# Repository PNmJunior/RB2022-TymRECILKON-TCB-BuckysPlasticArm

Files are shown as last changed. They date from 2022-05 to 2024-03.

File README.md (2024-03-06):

# Článek o vývoji robota BuckysPlasticArm

Robot BuckysPlasticArm je pojízdný robot s manipulačním ramenem. Sestavil jsem si ho, abych si vyzkoušel práci s webovým  serverem umístěným v ESP32 (ESP32DevKitV1 [^11]), který přes webserver  umožňuje řídit pohyb robota s osmi DC motory. Webserver poskytuje v lokální sítí webovou službu, přes  kterou jde z více webových prohlížečů najednou ovládat robota. 

Prakticky jsem si funkčnost robota ověřoval na soutěži Robotický den 2022 a 2023. [^2][^3]

## Historie projektu

### 1.Etapa 
S projektem jsem začal v březnu 2022 a mým cílem byl Robotický den 2022 konající se 5. a 6. června. [^1] Jako základ jsem vybral projekt s nazývem „ESP32 Web Server (WebSocket) with Multiple Sliders: Control LEDs Brightness (PWM).“ od „Random Nerd Tutorials“, který jsem našel na internetu, a který jsem upravil pro své potřeby.[^3] Šlo o ovládání tří parametrů LEDek. Zvětšil jsem množství ovládaných parametrů na osm. Každý ovládací parametr řídil jeden motor. Do původní webové stránky [^3] jsem přidal jak nové horizontální, tak i vertikální slidery (ovládací posuvný prvek v HTML(```<imput type="range">```)).[^10] Zjistil jsem, že z Androidů lze ovládat dva slidery najednou, zatím  co na počítači limitovaného  myší, šlo ovládat jen jeden slider. Můj plán byl umožnit řídit robota ze čtyř mobilních zařízení najednou v reálném čase pomoci týmů lidí. Kvůli řízení v reálném čase, jsem musel minimalizovat množství posílaných dat. Díky tomu jsem se dostal na odezvu robota v řádech desítek milisekund. Změnil jsem typ http serveru ze synchronního na asynchronní.

Na soutěži jsem si ověřil, že řízení pomocí více lidí je špatný nápad, kvůli jejích nutné vzájemné souhře.

### 2.Etapa
Technologie webserveru v ESP32 mě zaujala, a tak jsem se rozhodl pokračovat ve vývoji. Pustil jsem se do velké přestavby konstrukce robota, hardwaru a softwaru. Vytvořil jsem si jednoduchý ovládací panel, který mi umožňoval výběr WiFi a  zadání hesla pomoci enkodéru pro připojení k lokální síti. Pomoci segmentového LED displeje robot informoval o vlastní aktuální IP adrese v lokální síti. Vytvořil jsem si vlastní komunikační protokol mezi serverem a klienty. Přidal jsem do zobrazení webu čtyři joysticky se synchronizací (každý vidí, co dělají ostatní).[^7] Synchronizace sliderů byla už z původního projektů.[^3] Kód pro joystick, který byl napsaný v JavaScriptu, hýbal s obrázkem páčky. ESP32 převádělo pohyby joysticků na pohyb sliderů. Díky tomu šlo jedním kliknutím ovládat až dva motory najednou. Tím se mi snížil počet lidí s telefonem k ovládaní robota na dva. 

### 3.Etapa - Fyzické joysticky
Rozhodl jsem se, že umožním řízení zmíněných osmi motorů pomoci jednoho člověka. Pro tento účel jsem vyrobil dvojici fyzických joysticků (pro každou ruku), kde se zápěstím ovládá dolní joystick a druhý/horní joystick se ovládá pomoci palce. 

Po té jsem začal řešit spojení s robotem. Ano, šlo to jednoduše vyřešit dalším ESP32, ale to bych si nevyzkoušel nové technologie, a proto jsem se rozhodl, že použiju WebUSB.[^4] Pomoci desky Bluepill(deska s čipem ARM STM32 STM32F103C8 [^12]) jsem chtěl komunikovat s webovým klientem v prohlížeči právě přes USB. Zde jsem narazil na překážku v podobě bezpečnosti, kde bylo podmínkou použití protokolu https. Celý projekt do této doby fungoval přes http. Po nastudování dokumentace a různých diskusí jsem došel k názoru, že přeprogramovat ESP32 na https server by bylo možné. Ale mnohonásobně by se tím zvýšila doba odezvy až na sekundy. Zároveň by se snížil počet možných webových klientů z osmi na maximálně čtyři, co je na hranici plánovaného používaní.[^8] [^9] K řešení problému s bezpečností nepřispělo ani nahrávaní stránek z disku. Nakonec jsem musel použit aplikaci, která umožňovala převádět komunikaci z USB na Telnet napsané v Javě.[^5] Tento koncept jsem použil a zprovoznil, ale doba odezvy byla vysoká a tak jsem přeprogramoval aplikaci pro simulaci klienta.[^6] Tím jsem maximálně snížil dobu odezvy na pohyb joysticků. Můj protokol nebyl navržen pro stream, ale pouze pro paketovou přepravu. To mělo za následek, že jsem musel vyřešit na straně aplikace rozpoznávání zamýšlených paketů.

### Testování webu na konci 2.etapy a v průběhu celé 3.etapy 
Projekt jsem ladil pouze na prohlížeči Google Chrome pro platformy Windows a Android. K tomu se mi občas objevila možnost si kód otestovat na jiných zařízeních, platformách a prohlížečích. Díky tomu jsem zjistil několik zajímavých informací z pohledu kompatibility kódu. Při testovaní jsem se zaměřoval na funkce  sliderů a  softwarových joysticků. Testy s Mac a IOS byly prováděny pouze na prohlížeči Safari. U Androidu jsem provedl testovaní na Webview, Google Chrome a Firefox. Na Windows jsem to otestoval na  Webview, Google Chrome, Firefox a Edge. Na Linuxech jsem testoval Google Chrome a Firefox. Podle očekávaní se slider zobrazoval na různých prohlížečích trochu jinak(různá implementace HTML prvku).[^11] Překvapil mě rozdíl podpory zobrazení horizontálních a vertikálních sliderů v rámci stejného prohlížeče. Dokonce na Firefoxu mi vertikální slidery vůbec nefungovaly. Je ale důležité upozornit, že joysticky (manipulovaní s obrázkem) vždy fungovaly na všech prohlížečích správně a měly ten samý vzhled a chování.[^7]

Nalezl jsem článek, který popisuje tuhle problematiku. [^13] 

### 4.etapa
Znova jsem celého robota přestavěl konstrukčně a ještě před soutěží Robotický den 2023 [^2] jsem implementoval funkce pro kontrolu spojení. Na soutěži mi robot kvůli neustálé detekci rušení spojení přerušoval pohyb. Bohužel neměl jsem čas dostatečně vyladit tuhle kontrolu.

### Finální zakončení projektu
Po soutěži jsem vytvořil github větev def2024, kde je program bez funkcí kontroly spojení.

Pro vyladění kontroly spojení by bylo nutné téměř vše přeprogramovat. 

Odstranil jsem problémy řešené v kapitole „Testování webu na konci 2.etapy a v průběhu celé 3.etapy“ pomoci článku zabývající se slidery. [^13]

## Technický popis:

V projektu jsem si praktický ověřil a otestoval: 
- Poskytování webových služeb v lokální síti přes ESP32.
- Koncept řízení s více klienty najednou. 
- Řízení až 8 parametrů najednou z 4 klientů. 
- Kontrola spojení. 
- Napsání jednoduchého html/css/javascript kódu pro řízení a kontrolu nastavení jednotlivých ovládaných parametrů. 
- Otestoval jsem kombinaci různých druhů řízení a kontroly.
- Zkusil jsem si tvorbu vlastního komunikačního protokolu a jeho zefektivnění. 
- Upravil  jsem aplikaci v Javě, která emulovala chovaní klienta a analyzovala přeposílána data.

### Řízení z vice zdrojů (klient a jiné vstupy dat)
U řízení z více zdrojů jsem došel k závěru, že nejprve je nutné popsat druhy a množství vstupních zdrojů. Dají se rozdělit na dva typy: Jednosměrné a synchronní.

#### Jednosměrné řízení
Jednosměrné jsou ovladače bez zpětné vazby, a proto nelze si ověřit aktuálnost dat a žádná data se nezobrazují ani nijak nezpracovávají. Kvůli zjednodušení lze je považovat za direktivní, informace s maximální prioritou nelze ignorovat. To znamená, že synchronní řízení podléhá přímému řízení.

#### Synchronní řízení
Synchronní řízení je typické pro web s klienty. Lze řídit a vidět, co dělají ostatní.

Kolize pokynů nebo strata spojení nebo následná kombinace obojího je velký problém. Například když klient dá parametr na 100% a následně se přeruší spojení, je nutné buď nastavit parametr na 0 nebo nechat jiného klienta převzít řízení. Zároveň detekce ztráty spojení pro ESP32 je taky dost náročná na výkon. Dalším problémem je situace, kdy dva klienti ovládají stejný parametr. Další situace je když jeden klient ovládá parametr a přeruší se spojení na určitou dobu. Je nutné, aby detekce spojení umožnila jinému uživateli převzít řízení a následně, aby vyřešila situaci s náhlým množstvím expirovaných instrukcí z původního klienta.

### Kontrola spojení
Kontrola spojení u synchronních zdrojů je nutností kvůli řízení v reálném čase. Kvůli analýze spojení je nutné neustále posílat alespoň datový paket s informací o čase. Následně je otázka, jak zareagovat na pakety, které jsou starší než by měly být. Pro ESP32 je velmi náročné přijímat neustále data od vice klientů, je zde velká pravděpodobnost zahlcení a častého restartovaní.

### Jednoduchý kód pro web na různých platformách
Prakticky jsem si vyzkoušel tvorbu ovládacích prvků pomocí obrázků a JavaScriptu. Rozhodl jsem se nespoléhat na ovládací prvky v HTML a na platformně závislé funkce v JavaScriptu. Pokud si to naprogramujete pomocí základních JavaScriptových funkcí, tak vzhled a chování by mělo být jednotné na mnoha platformách po dlouhou dobu. Slidery se v každém prohlížeči zobrazovaly a chovaly jinak. Zatímco kód emulující joysticky [^7] s grafikou pomoci obrázků vždy se choval a vypadal stejně. Vice v předchozí kapitole Historie-Testování.

### Komunikační protokol mezi serverem a klienty

#### Původní protokol
Nejprve jsem použil komunikační protokol z původního projektu, založený na JSON.[^3] Tento protokol byl velmi popisný, proto vyžadoval velké množství dat. Data pro osm parametrů se museli dělit do dvou paketů, co značně zpomalovalo komunikaci. 

#### Optimalizace protokolu
Nejprve jsem optimalizoval množství posílaných dat. Upravil jsem protokol tak , že na místo posílání klíčového slova jsem posílal jen jedno písmeno. Tím jsem celkovou velikost snížil na jeden paket při osmi parametrech.

#### Vlastní protokol
Můj protokol byl textový a měl dva klíčové znaky:
- „;“ pro zahájeni balíčku, 
- „:“  rozdělení jednotlivých subbalíčků o různém počtu.

Balíček obsahoval soubor subbaličků, kde první subbalíček určoval typ informace(příkaz) a z toho se odvodil následný počet subbalíčků. V jednom paketu mohlo být více balíčků. Díky TCP funkcím v ESP32 se vždy server začal zabývat daty až když byly kompletní. Díky tomu nebylo nutné implementovat koncový znak. 

#### Problémy
Při komunikaci přes USB mezi aplikací a Bluepill([^12]), který snímal polohu mechanických joysticků, jsem musel vkládat specifické balíčky. Na začátek a konec každého posílaného myšleného paketu ze strany Bluepill, jsem vložil balíček, aby aplikace jej mohla identifikovat a celý ho poslat.

## Závěr

Na tomto projektu jsem si otestoval mnoho technologií a postupů. Vzhledem ke komplikovanosti problematiky serverů z pohledu bezpečnosti a výkonu, jsem se rozhodl si vytvořit nový projekt zabývající se částečným převodem povinností serveru na aplikaci, která by s ESP32 komunikovala přes Bluetooth.

## Zdroje:
Zdroje jsou zobrazené na konci README.md

[^1]: Robotic Day 2022 [online]. 2022 [cit. 2024-02-15]. Dostupné z: http://robotickyden.cz/2022/

[^2]: Robotic Day 2023 [online]. 2023 [cit. 2024-02-15]. Dostupné z: http://robotickyden.cz/2023/

[^3]: ESP32 Web Server (WebSocket) with Multiple Sliders: Control LEDs Brightness (PWM). Random Nerd Tutorials [online]. 2021 [cit. 2024-02-15]. Dostupné z: https://randomnerdtutorials.com/esp32-web-server-websocket-sliders/

[^4]: Access USB Devices on the Web. Chrome for developers [online]. [cit. 2024-02-15]. Dostupné z: https://developer.chrome.com/docs/capabilities/usb

[^5]: CLUSTER, Alexey. USB Serial Telnet Server. GitHub [online]. [cit. 2024-02-15]. Dostupné z: https://github.com/ClusterM/usb-serial-telnet-server.git

[^6]: ŇACHAJ, Pavol. USB Serial Telnet Server. GitHub [online]. 2023 [cit. 2024-02-15]. Dostupné z: https://github.com/PNmJunior/usb-serial-telnet-server.git

[^7]: STEMKOSKI. Touch-enabled Virtual JoyStick Controller In JavaScript. CSS Script [online]. 2020 [cit. 2024-02-16]. Dostupné z: https://www.cssscript.com/touch-joystick-controller/

[^8]: HESSEL, Frank. ESP32 HTTPS Server. GitHub [online]. [cit. 2024-02-22]. Dostupné z: https://github.com/fhessel/esp32_https_server.git

[^9]: HTTPS server. ESPRESSIF [online]. [cit. 2024-02-22]. Dostupné z: https://docs.espressif.com/projects/esp-idf/en/release-v4.4/esp32/api-reference/protocols/esp_https_server.html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

[^10]: ```<input type="range">```. Mdm [online]. [cit. 2024-02-26]. Dostupné z: https://developer.mozilla.org/en-US/docs/Web/HTML/Element/input/range

[^11]: PK-DevKitV1 Esp32. PROKYBER s.r.o. [online]. [cit. 2024-02-26]. Dostupné z: https://e-shop.prokyber.cz/esp32/esp32-pkdevkitv1/

[^12]: BluePill ARM STM32 STM32F103C8 Vývojová deska. LaskaKit [online]. [cit. 2024-02-26]. Dostupné z: https://www.laskakit.cz/bluepill-arm-stm32-stm32f103c8-vyvojova-deska/

[^13]: Stylování ```<input type=range>```. JAHODA, Bohumil. JE ČAS [online]. 2023 [cit. 2024-03-05]. Dostupné z: https://jecas.cz/input-range

---

---

Původní verze úvodu:

# BuckysPlasticArm

Robota BuckysPlasticArm jsem vždy koncipoval jako prostředek k rozvíjený znalostí v oblasti IOT. Robot je řízen přes webové rozhraní v kombinaci s joysticky. Veškerá komunikace je vedena přes webserver umístěný na robotovi v podobě ESP32, který zároveň ovládá celého robota.
Zapojení webserveru má svoje výhody ale i nevýhody. Jednou nespornou výhodou je možnost se podílet více zařízeními na ovládání robota. Navíc se stačí jen připojit do stejné sítě a v prohlížeči zadat ip adresu, kterou ukazuje robot. 
Nevýhodou není ani webserver, ale spojení přes wifi, která není stavěná na spojitou komunikaci. To značně komplikuje situaci webserveru. 
Nesmím zapomenout na historii robota. Tento robot se jako rychlo projekt zúčastnil minulý rok Robotického dne na disciplíně Toy Cleanup Beginner. Za dobu existence robota už měl tři různé konstrukce, dva různé hardwary a nekonečně uprav v softwaru. Přírůstkem jsou joysticky. Toto zařízení má čtyři joysticky PS4 a signál zpracovává STM32, které posílá data přes mobilní aplikaci, mnou modifikovanou, přes router do robota. Je úplné k nevíře, že řízení pomoci webu a joysticků je v reálném čase.
Robot je sestaven pomoci stavebnice KSR10. 
[Základy projektu](https://randomnerdtutorials.com/esp32-web-server-websocket-sliders/)

## QR
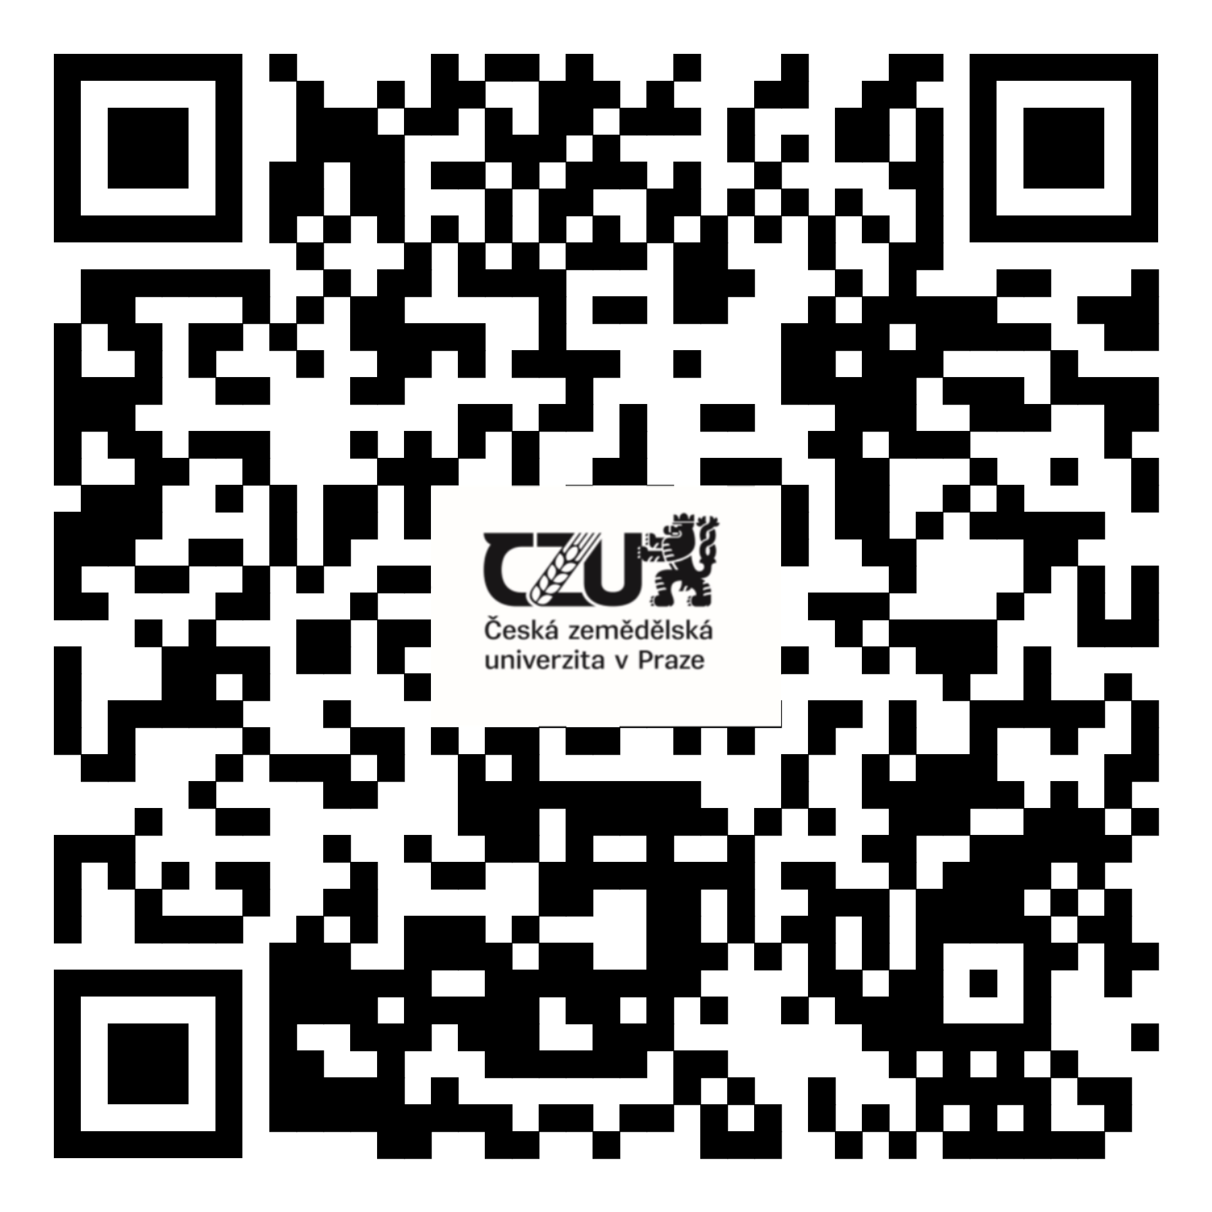
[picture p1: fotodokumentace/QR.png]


## Aktuápní podoba

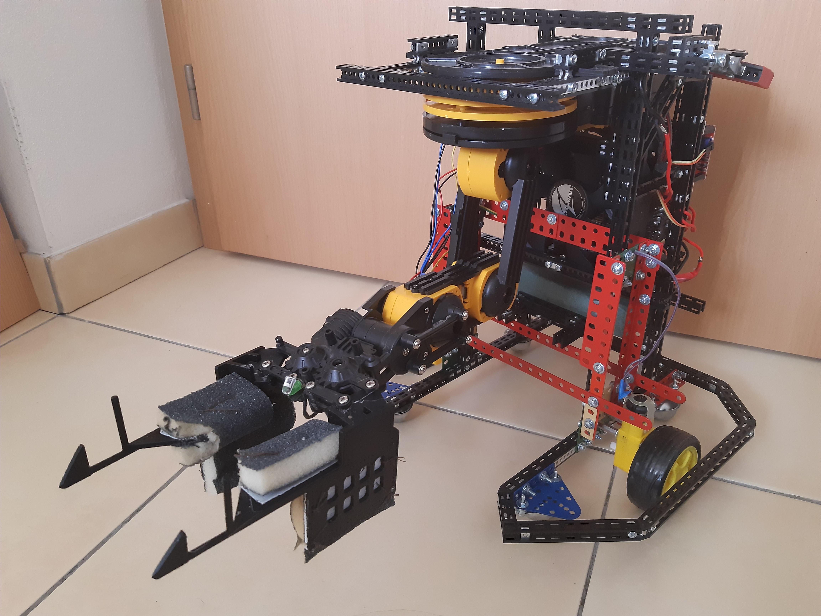
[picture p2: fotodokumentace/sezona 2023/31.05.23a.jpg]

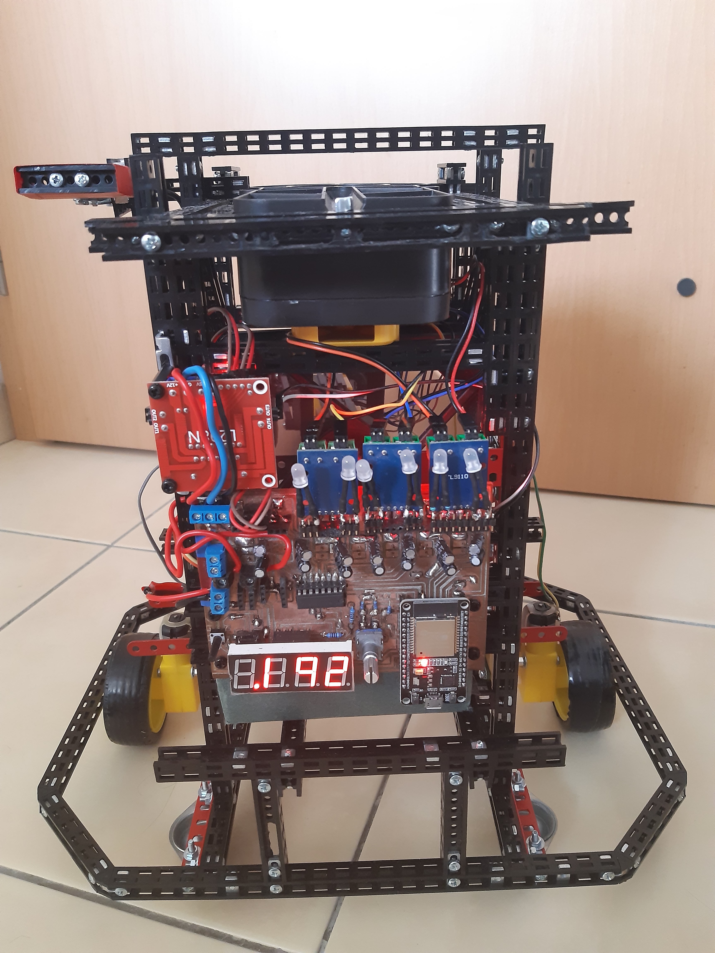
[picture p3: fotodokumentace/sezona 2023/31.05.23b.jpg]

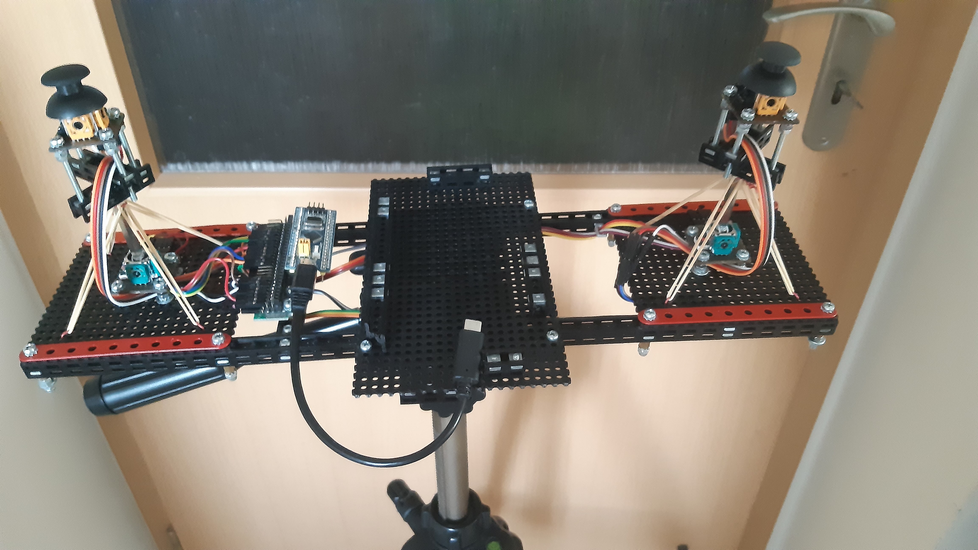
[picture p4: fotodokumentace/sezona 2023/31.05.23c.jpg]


# Popis větví projektu
## [main](https://github.com/PNmJunior/RB2022-TymRECYLKON-TCB-BuckysPlasticArm/tree/main) 
Hlavní větev pro práci.
## [Telnet](https://github.com/PNmJunior/RB2022-TymRECYLKON-TCB-BuckysPlasticArm/tree/Telnet) 
Značně propracovaná větev, ale kvůli pomalé rychlosti uzavřena. Tato technologie pomohla mi překlenou období mezi neúspěchem s https a přepsáním [aplikace](https://github.com/PNmJunior/usb-serial-telnet-server/tree/java-android-websocket-client) používané právě pro Telnet, kde jsem přidal připojovaní se pomoci webSocketu s serverem robota a zpracování dat z USB. 
Funkční. Práce ukončeny.
## [https-server](https://github.com/PNmJunior/RB2022-TymRECYLKON-TCB-BuckysPlasticArm/tree/https-server) 
Marný pokus o zprovoznění https-serveru proto, abych mohl použít [WebUSB](https://developer.chrome.com/articles/usb/) . Použití by znamenalo značné prodlevy v komunikaci. K samotné zkoušce WebUSB jsem se v této větvi nedostal. 
Nefunkční. Prace pozastaveny.
## [UsbWeb-opening-from-file](https://github.com/PNmJunior/RB2022-TymRECYLKON-TCB-BuckysPlasticArm/tree/UsbWeb-opening-from-file) 
Pokus o spuštění webové aplikace s [WebUSB](https://developer.chrome.com/articles/usb/) pomoci klikaceného souboru HTML. Tím jsem chtěl obejit bezpečnost bránicí požití WebUSB z http. Nastali problémy, které jsme nedokázal vyřešit. 
Nefunkční. Práce ukončeny.
## [http-server](https://github.com/PNmJunior/RB2022-TymRECYLKON-TCB-BuckysPlasticArm/tree/http-server) 
Funkční verze k 24.únoru 2023
## [Roboticky-den-2022](https://github.com/PNmJunior/RB2022-TymRECYLKON-TCB-BuckysPlasticArm/tree/Roboticky-den-2022) 
Soutěžní a funkční verze k 16.řijen 2022
## [main2](https://github.com/PNmJunior/RB2022-TymRECYLKON-TCB-BuckysPlasticArm/tree/main2) , [main3](https://github.com/PNmJunior/RB2022-TymRECYLKON-TCB-BuckysPlasticArm/tree/main3) 
Historické. Nedoporučuji čerpat. Uzavřeno. Nefunkční.

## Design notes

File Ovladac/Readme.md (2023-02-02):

# Ovladač
Jde o zařízení s možností ovládat všech osm motorů tak, aby to zvládal jeden člověk.
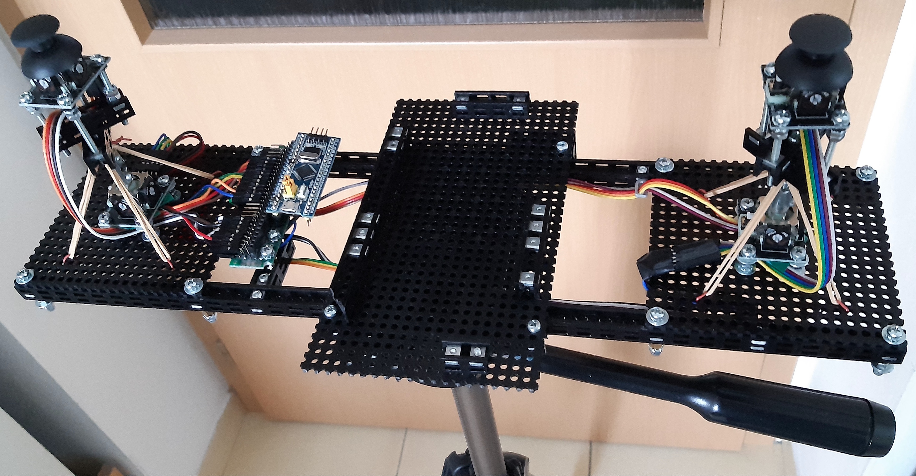
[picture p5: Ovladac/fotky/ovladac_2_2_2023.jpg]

Se stativem
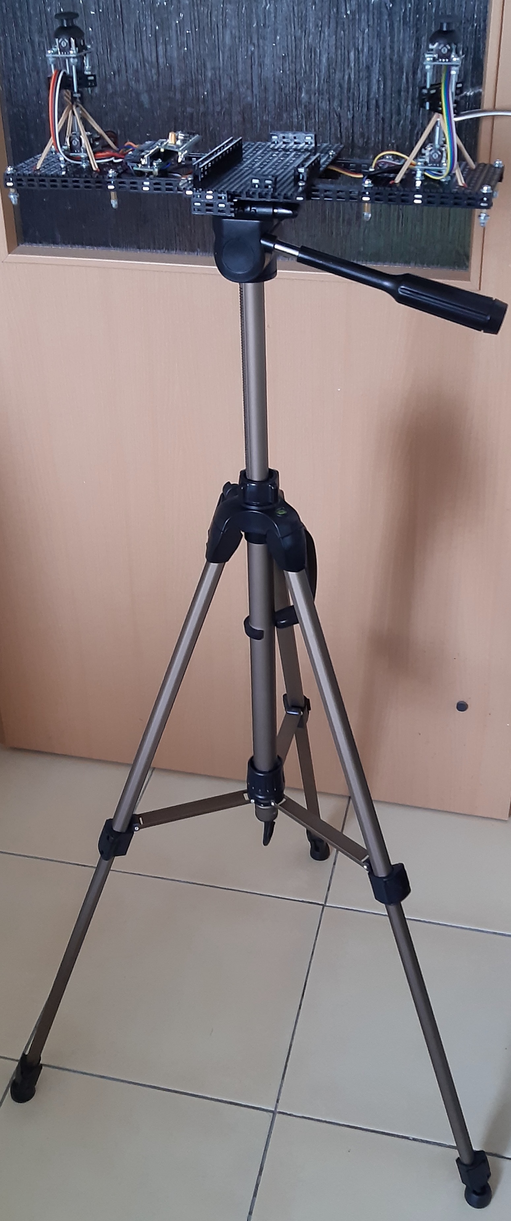
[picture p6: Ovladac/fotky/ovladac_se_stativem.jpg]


## Zapojení
Použil jsem levné Arduino joysticky. Úrovně napětí bude snímat BluePill a posílat data do telefonu přes USB.

## Komunikace
Přes USB pomoci Seriálové linky. V telefoně v Chrome bude tyto data přijímaný přepočítávany a posílána do robota jako pokyny sliderů.
https://developer.chrome.com/articles/usb/

## Koncept
Pochopil jsem, že nejlepší bude vyrobit pákový joystick v rámci kterého bude ještě jeden joystick pro prst.
Pravý Pákovy = Pohon.
- levý motor = vzorec zatím nevyvinut.
- pravý motor = vzorec zatím nevyvinut.

Levý Pákovy = Rameno.
- M1 = osa x.
- M2 = osa y.

Levý Horní = Rameno.
- LED = osa x.
- M3 = osa y.

Levý Horní = Rameno.
- Kleste = osa x.
- M4 = osa y.
    
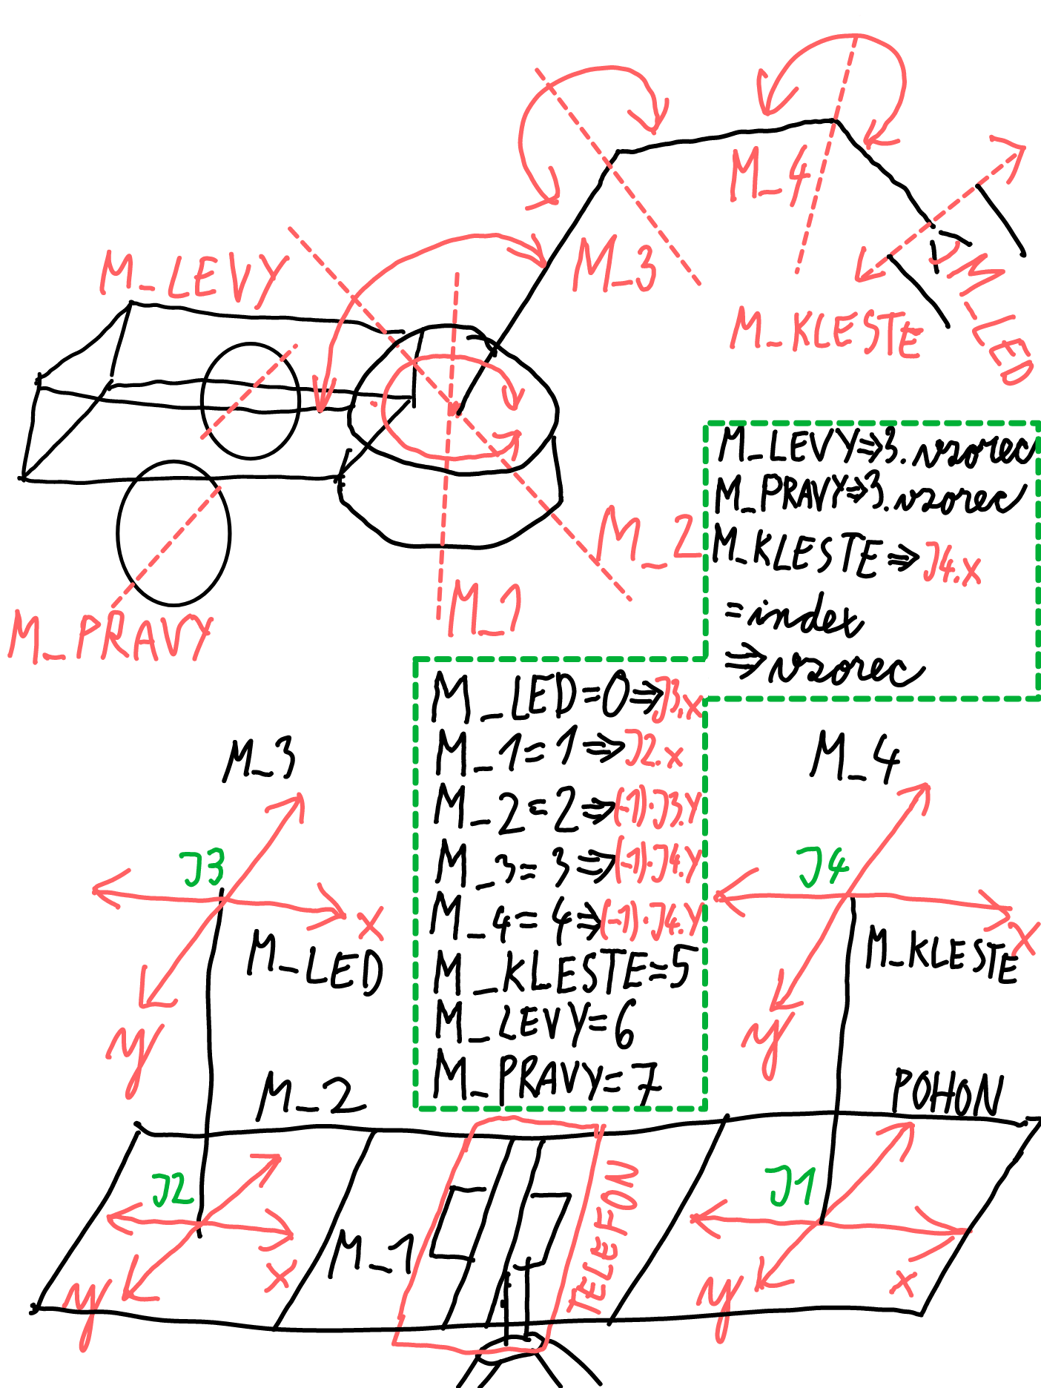
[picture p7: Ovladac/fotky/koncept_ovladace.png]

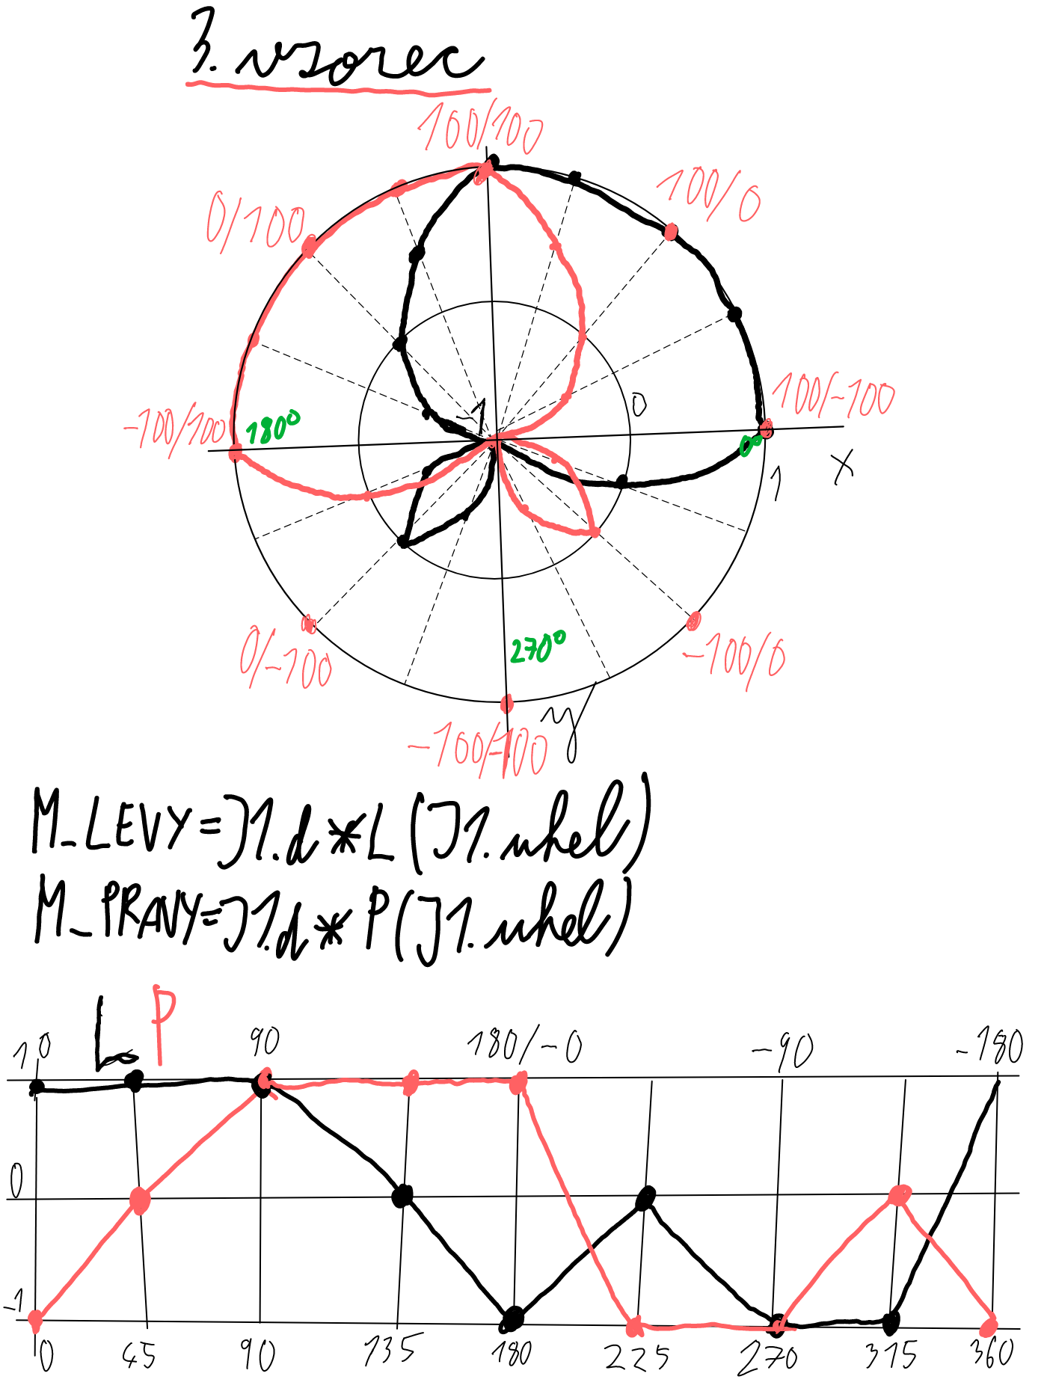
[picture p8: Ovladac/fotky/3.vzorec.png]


## Jednotka joysticku
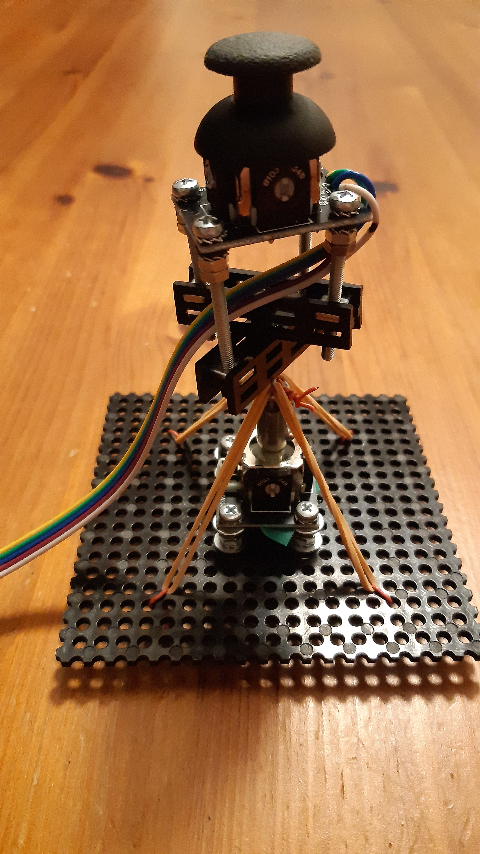
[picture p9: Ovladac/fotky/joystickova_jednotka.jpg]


## Modul pro telefon
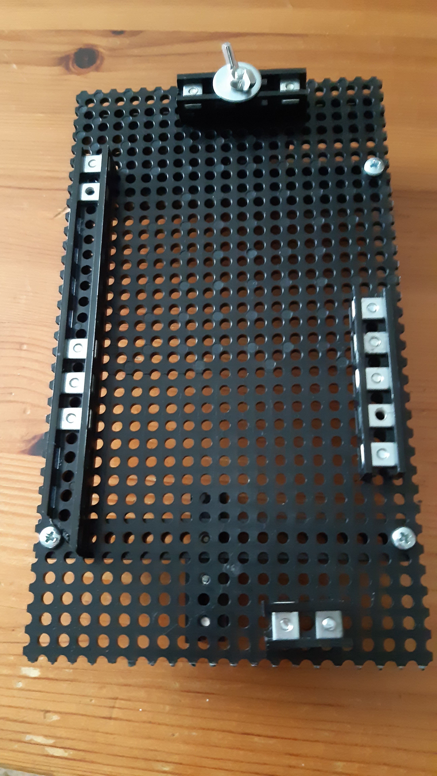
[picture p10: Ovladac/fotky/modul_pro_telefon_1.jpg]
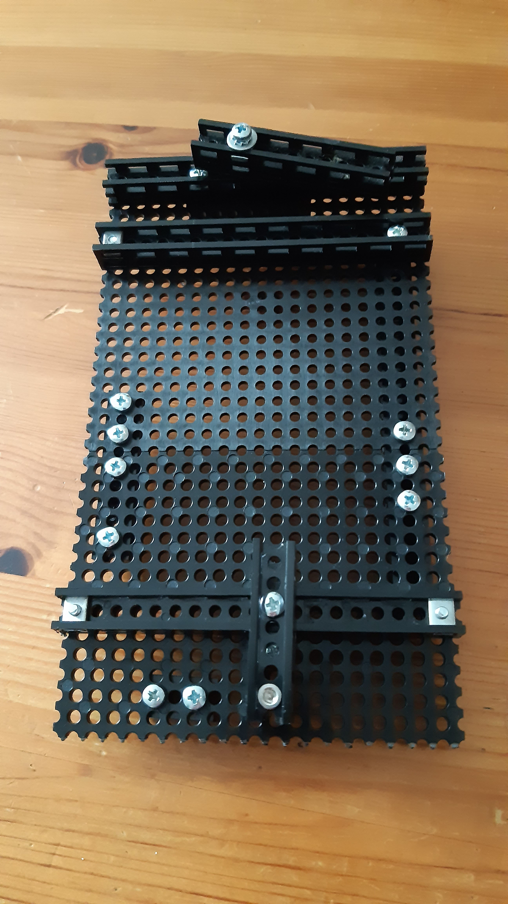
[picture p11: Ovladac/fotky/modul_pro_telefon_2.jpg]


## Rychloupínák na stativ
Nákres
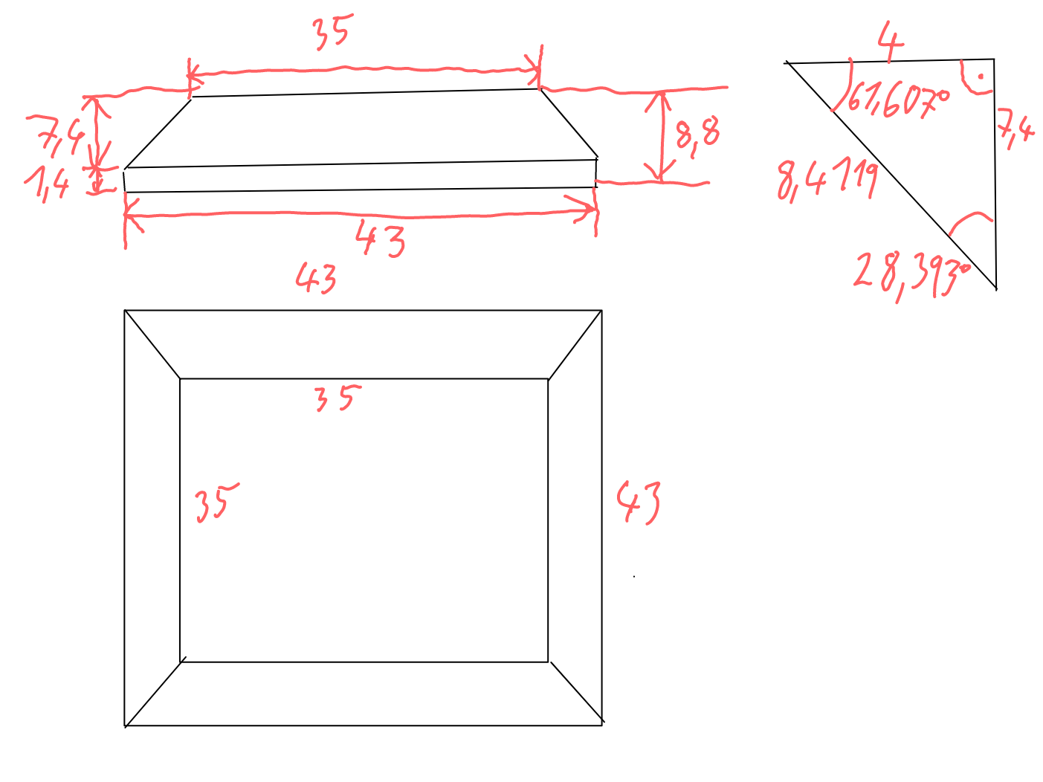
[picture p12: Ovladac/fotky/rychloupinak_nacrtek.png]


## Schéma
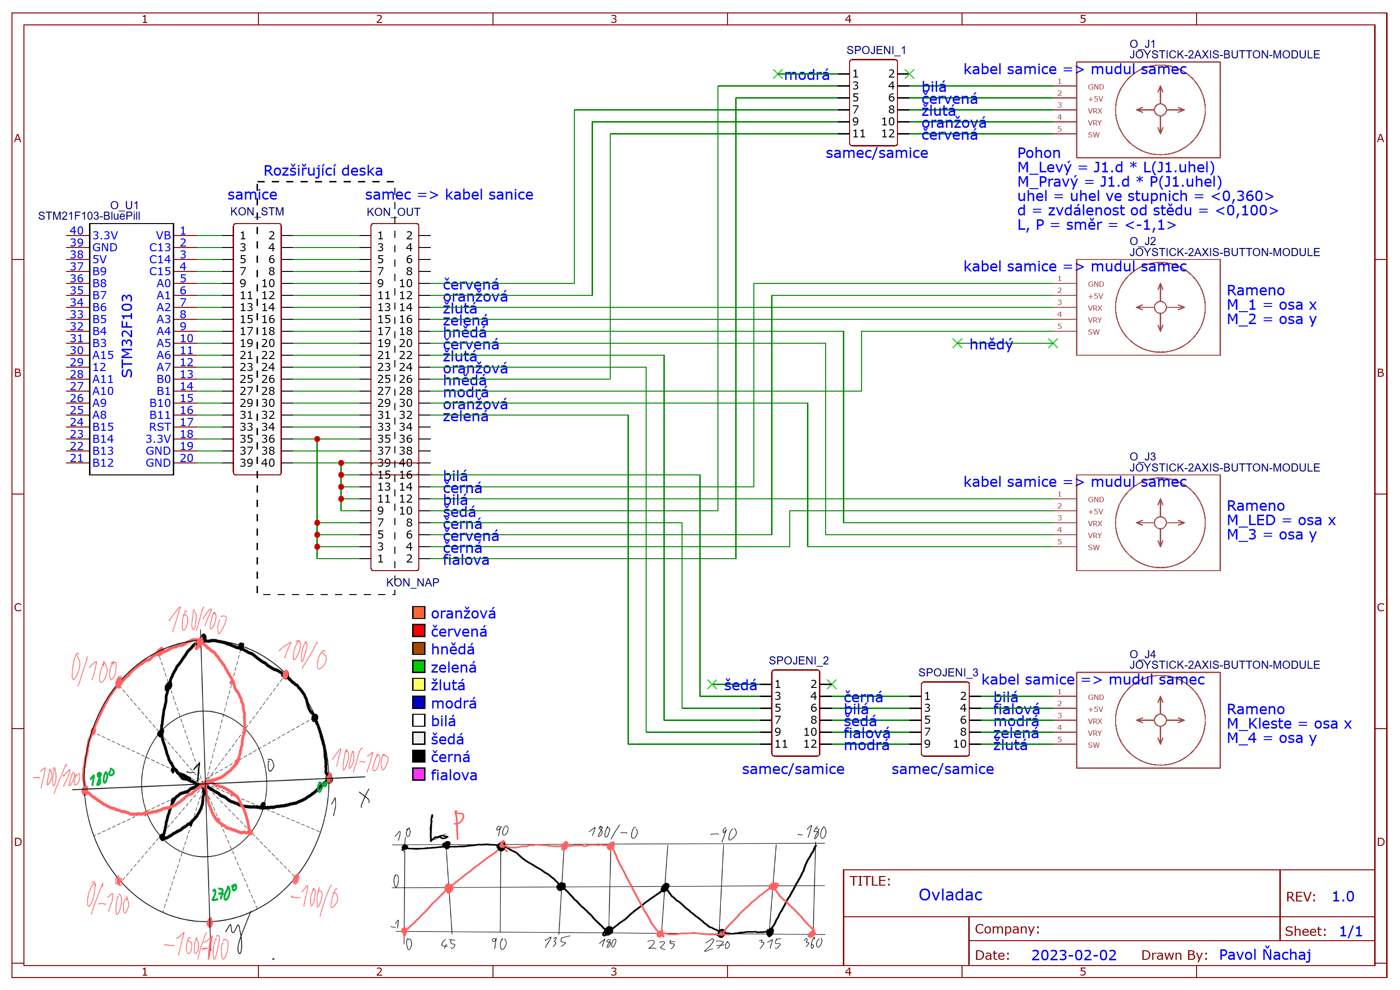
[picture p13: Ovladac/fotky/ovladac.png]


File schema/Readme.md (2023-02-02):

# Schéma
Pro tvorbu Schémy a PCB jsem použil [EasyEDA]https://easyeda.com/).

Kompletní schéma je zde:
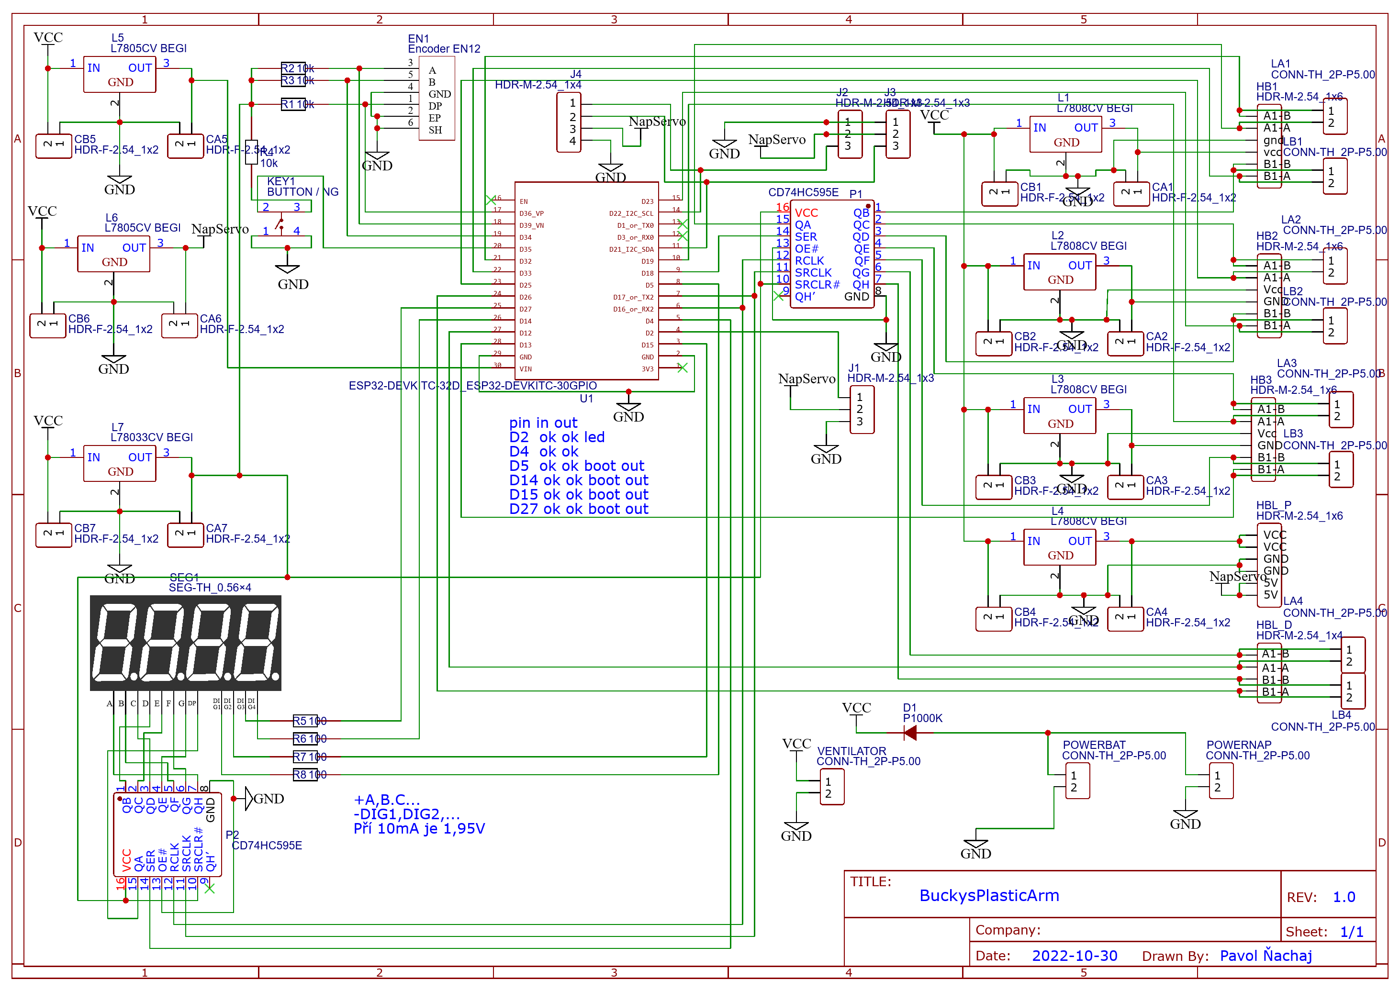
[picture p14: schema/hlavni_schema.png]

A komponenty:
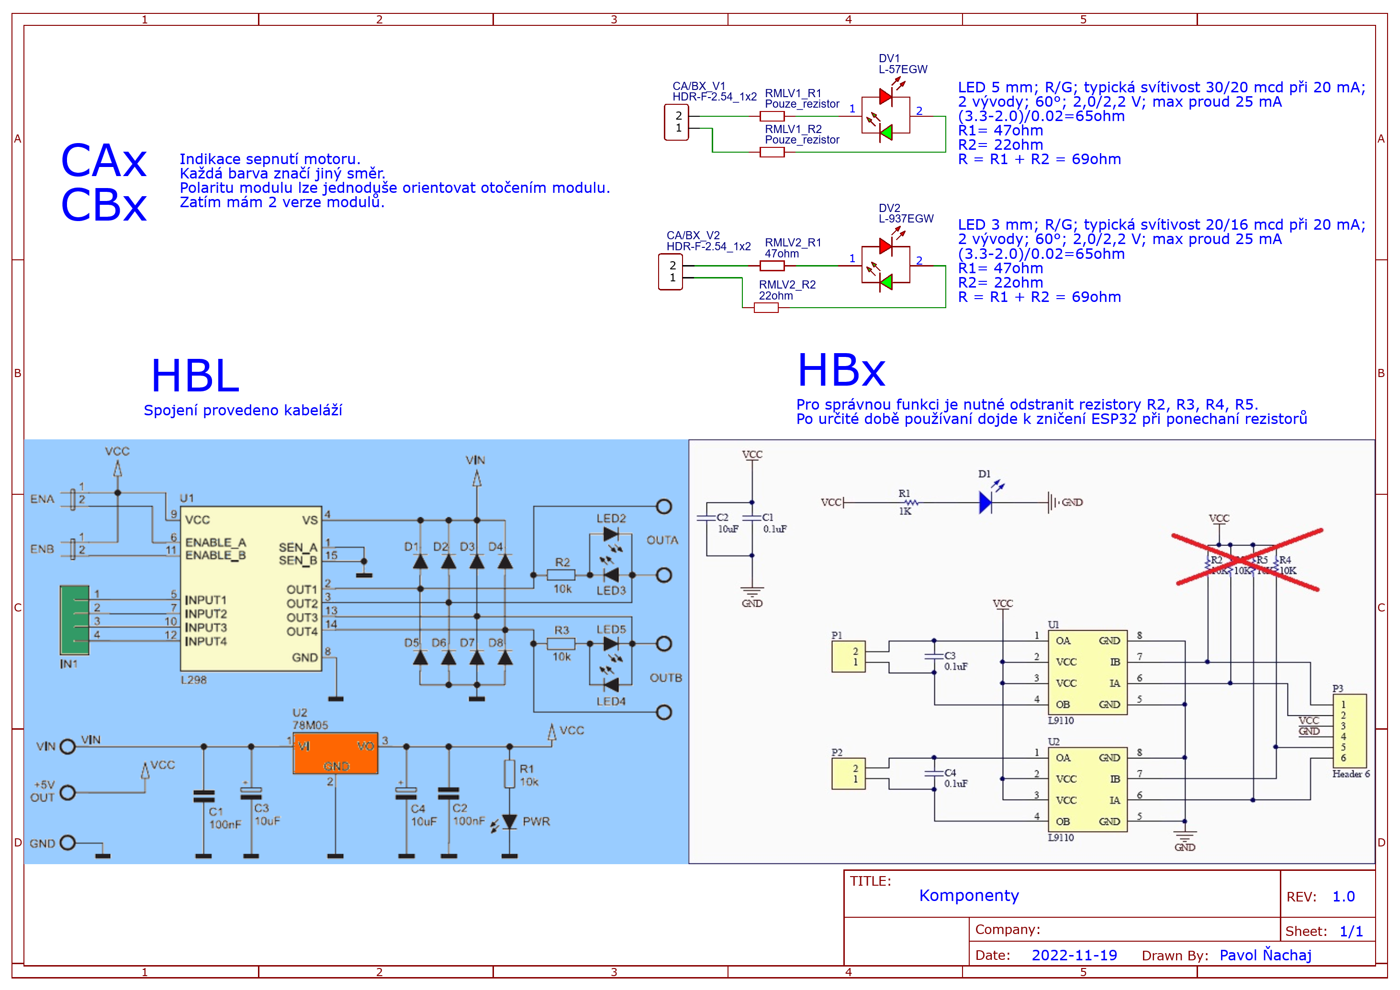
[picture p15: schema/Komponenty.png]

Ovladač:


# PCB

Pro výrobu PCB jsem použil návrh s názvem "PCB vyroba".

Šlo o prototyp, a tak jsem zde měl několik chyb. Zapomněl jsem svorku pro vypínač. A potom několik kosmetických záležitostis. Částečně opravenou verze mám pod názvem "PCB uprava1".

Fotka PCB zhora

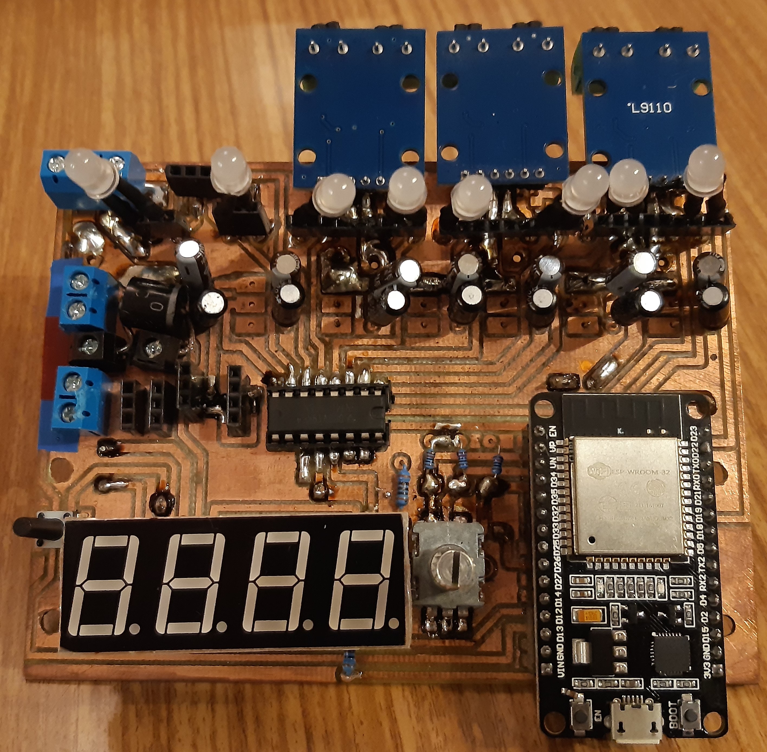
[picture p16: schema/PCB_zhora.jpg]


Fotka PCB zdola

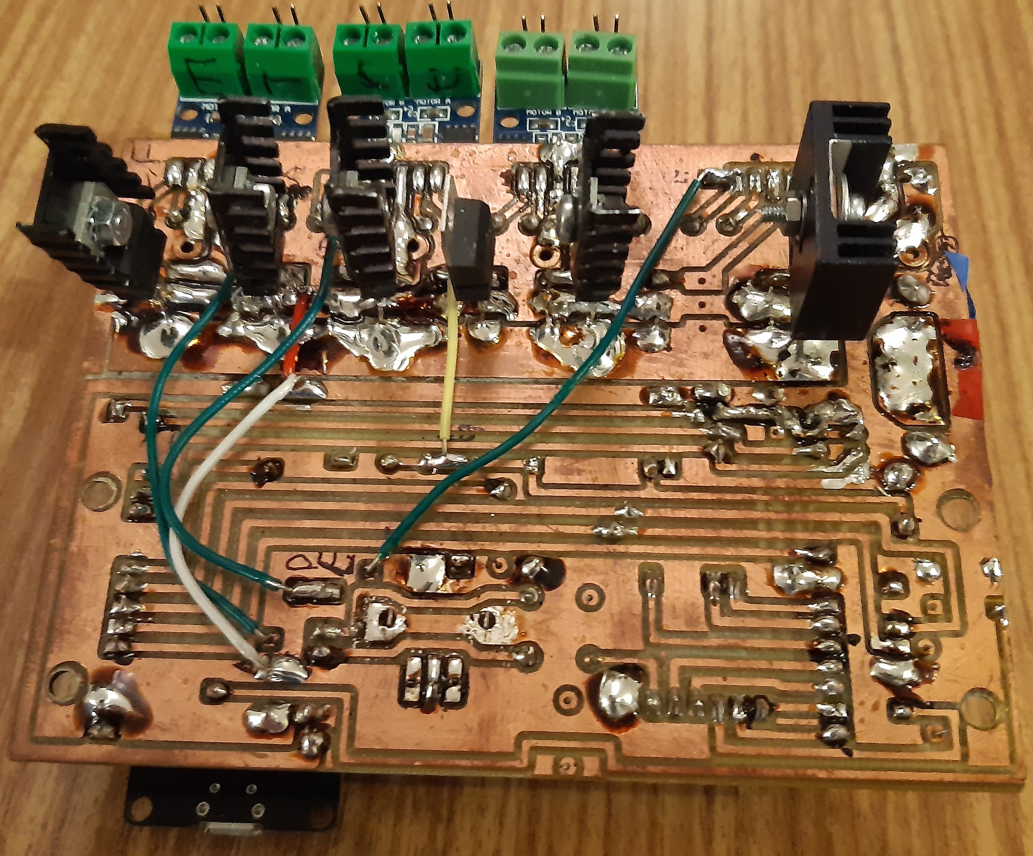
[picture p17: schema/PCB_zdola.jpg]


# Úpravy

Místo ochranné diody jsem umístil svorkovnici, kde umístím obvod, kde v sérii bude dioda a vypínač. Zatím je zde pouze dioda.

Chybí zde HBL (modul s L298N) pro řízení podvozku.

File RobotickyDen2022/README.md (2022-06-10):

# Závěr Ročníku 2022
Na robotový po softwarové stránce je vždy co děla.
Hardwarové jsem narazil na slabinu propojováních kabelů, které sem na vše použil. Problém byl s špatnými kontakty, tak i s vyhořením kabelu při proudových špičkách.

# Cíl na další rok
Doladit/překopat webové ovládaní.
Vytvořit plošný spoj.

# Fotky soutěžního robota
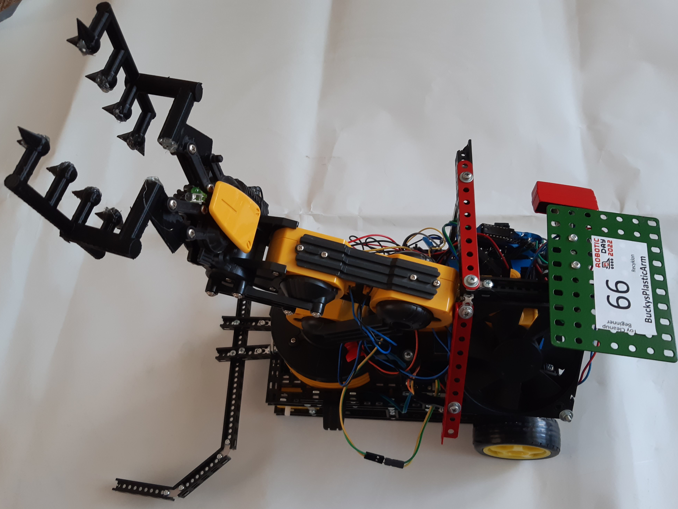
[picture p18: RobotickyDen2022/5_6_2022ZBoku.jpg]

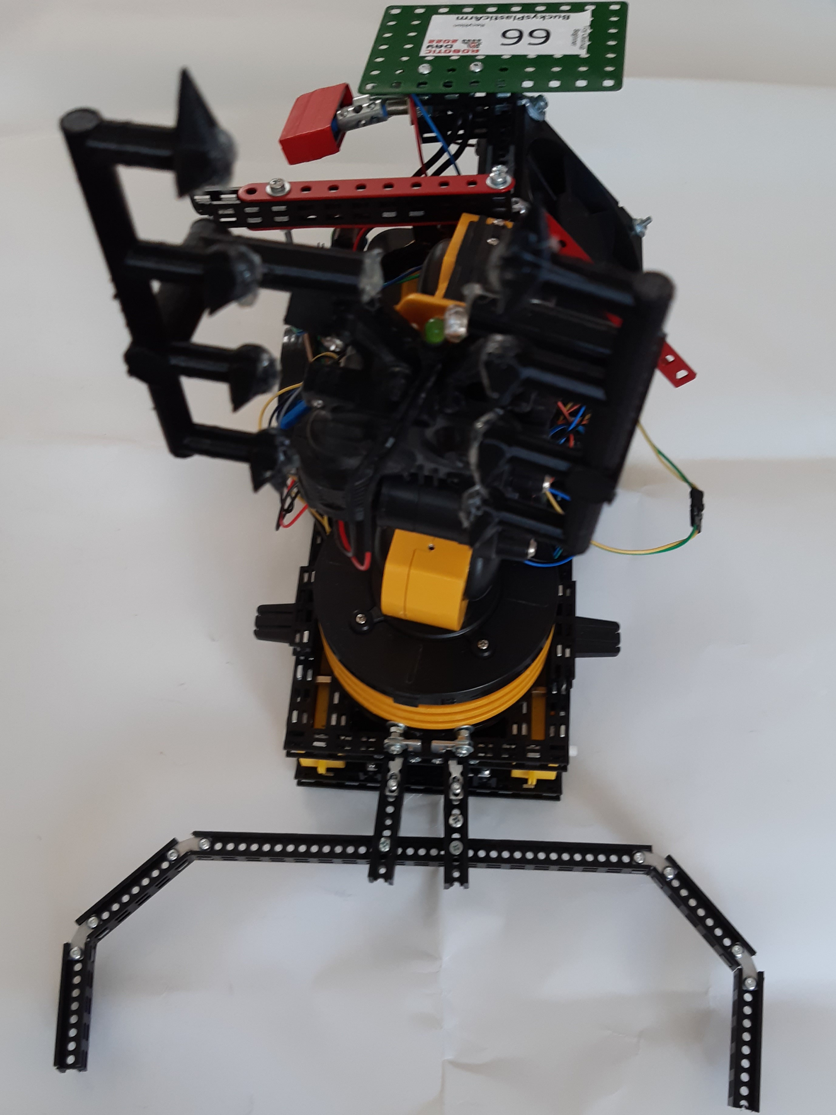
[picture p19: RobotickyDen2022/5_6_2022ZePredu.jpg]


# BuckysPlasticArm
Kategorie: Toy Cleanup Beginner
BuckysPlasticArm je robot, ve kterém jsem použil Robotické rameno KSR10. Přidal jsem k němu podvozek z Totemu a řídicí elektroniku. Hmotnost je 1,5kg. Robot zažil hned několik změn konceptů. Některé se dostaly i do gitu: https://github.com/PNmJunior/RB2022-TymRECYLKON-TCB-BuckysPlasticArm.git Posledním konceptem je, že v podvozku je dobíjecí baterie z notebooku a v původním prostoru pro baterie je elektronika. 
Původně jsem chtěl robota ovládat pomocí Bluetooth a mnou naprogramované mobilní aplikace. S tímto způsobem jsem ale měl špatné předchozí zkušenosti a tak jsem se rozhodl vyřešit to lépe. Zrušil jsem aplikaci, konstrukčně vyřešil bezdrátové bootování a řídil to pomocí webového prohlížeče. Kvůli použitým propojovacím kabelům k elektrickému propojení, jsem musel nadzvednout horní stranu krabičky o 2 centimetry, čímž jsem vyřešil i problém s chlazením.

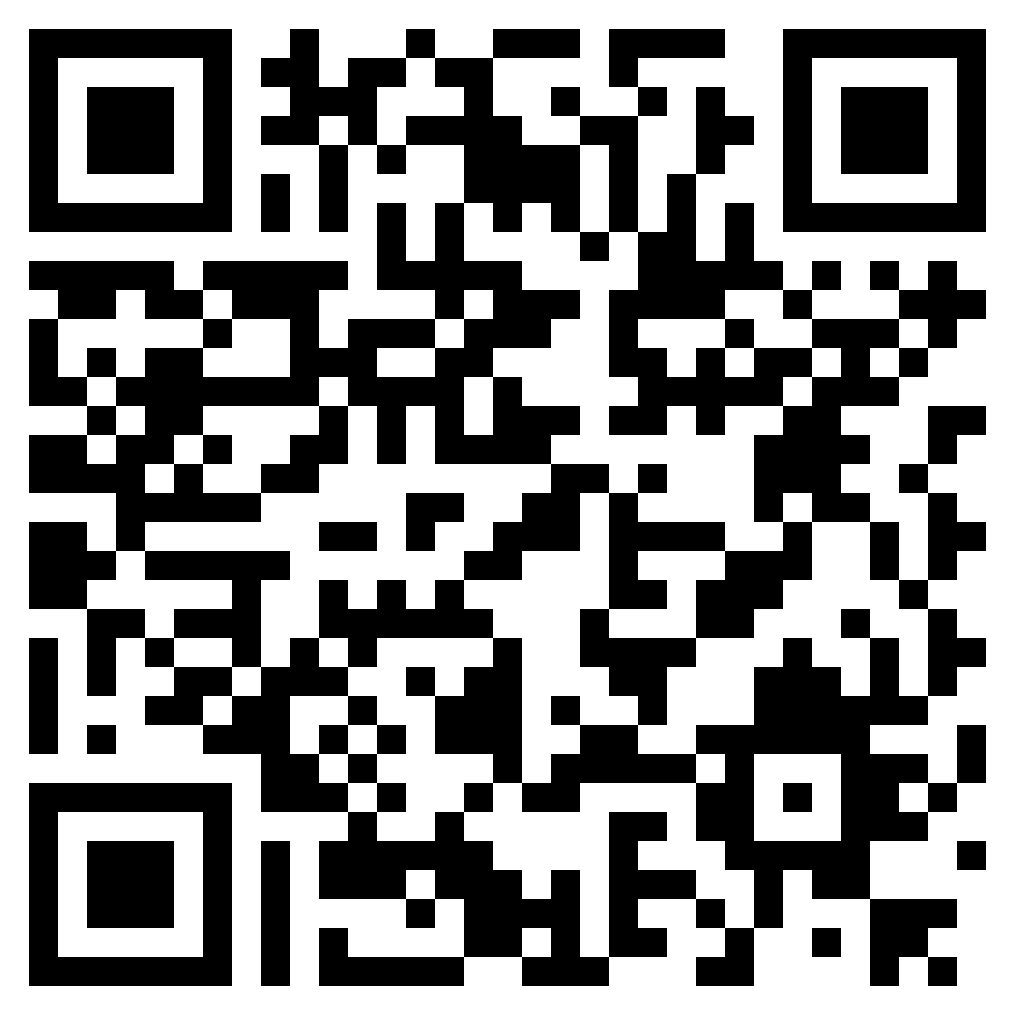
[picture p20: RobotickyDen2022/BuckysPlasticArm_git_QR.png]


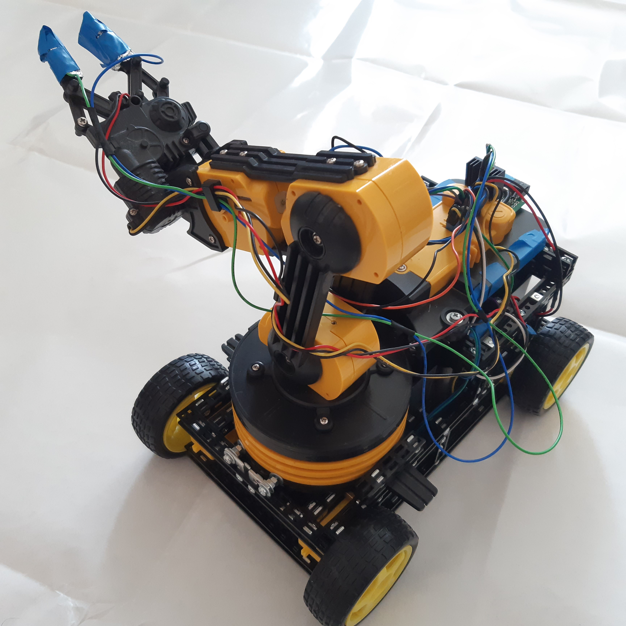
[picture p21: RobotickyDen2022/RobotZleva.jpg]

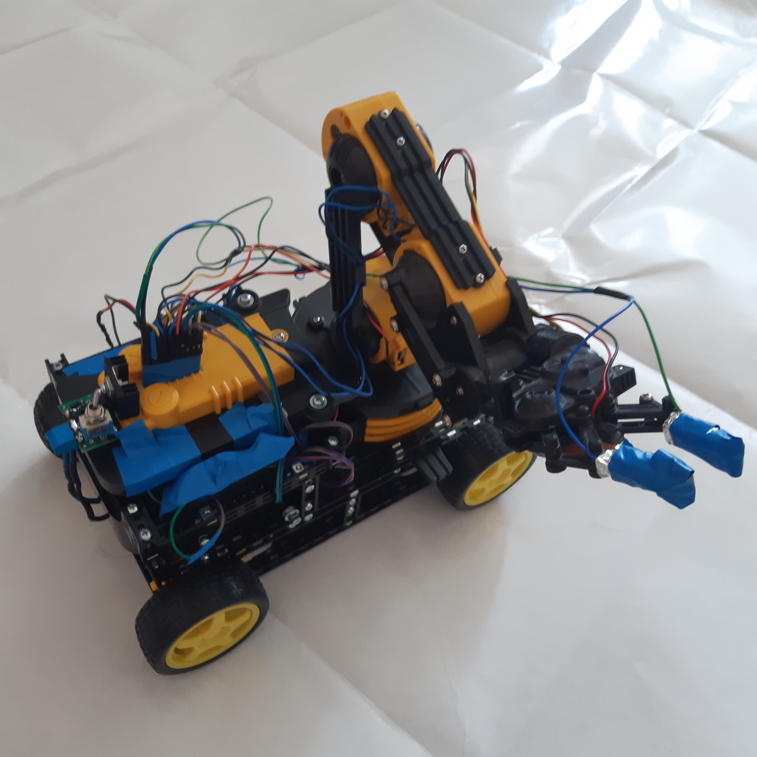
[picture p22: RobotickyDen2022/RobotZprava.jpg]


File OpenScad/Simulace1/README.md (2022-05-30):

# Simulace1
Test uchycení podélné kostky.
Test manipulace při kostce podélné.
Optika je 2D kvůli názornosti.

# Rozteč 0,0mm
Nereálné stavy.
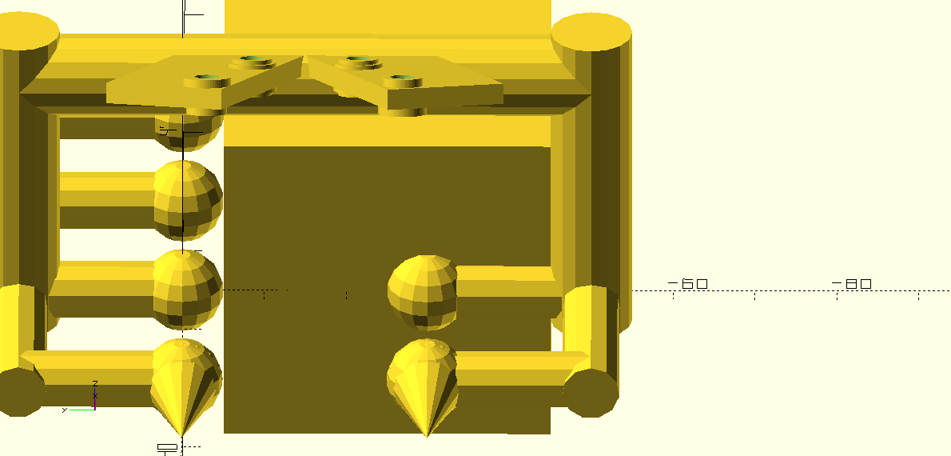
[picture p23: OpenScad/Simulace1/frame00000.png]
 

# Rozteč 4,5mm
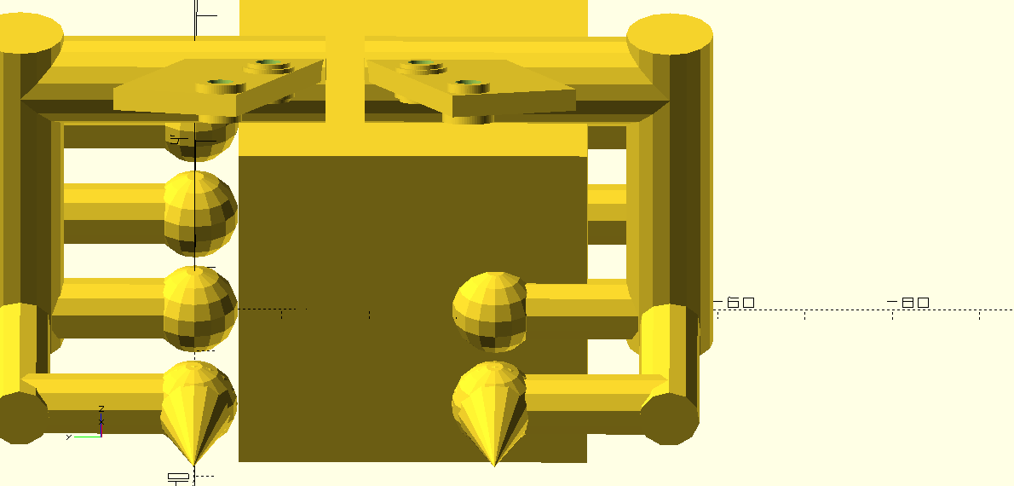
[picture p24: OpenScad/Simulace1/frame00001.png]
 

# Rozteč 9,0mm
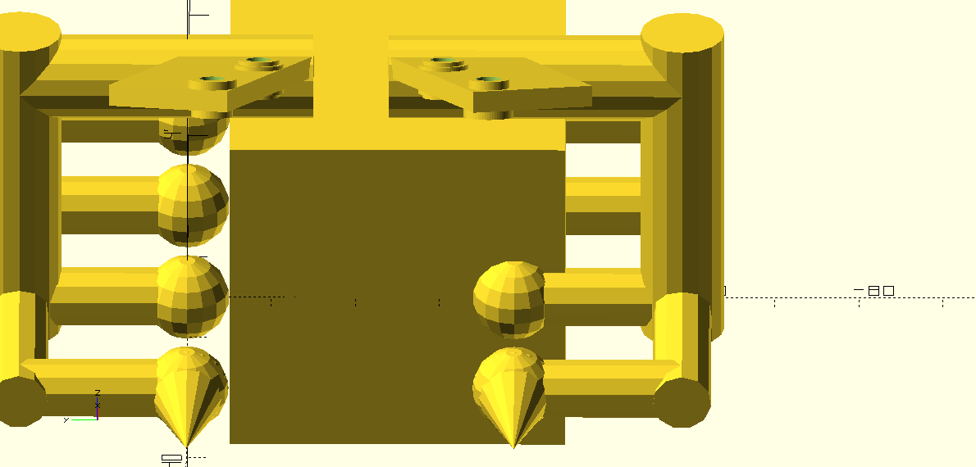
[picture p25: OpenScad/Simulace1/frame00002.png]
 

# Rozteč 13,5mm
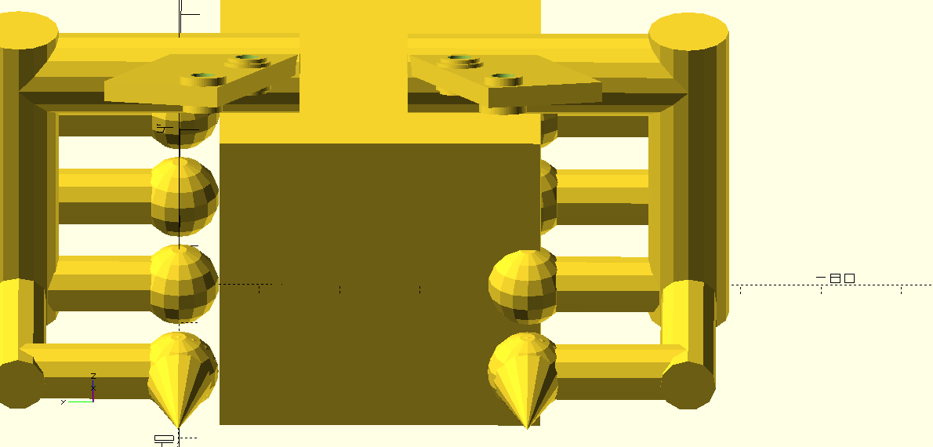
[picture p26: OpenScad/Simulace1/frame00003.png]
 

# Rozteč 18,0mm
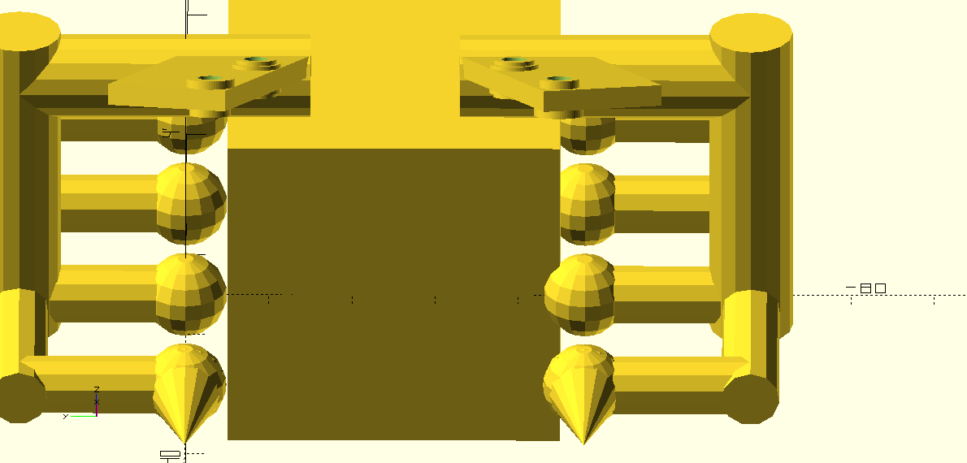
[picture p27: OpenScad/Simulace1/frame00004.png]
 

# Rozteč 20,0mm
Docházý k upevnění.
Větší rozteč už nedrží kostku.
# Rozteč 22,5mm
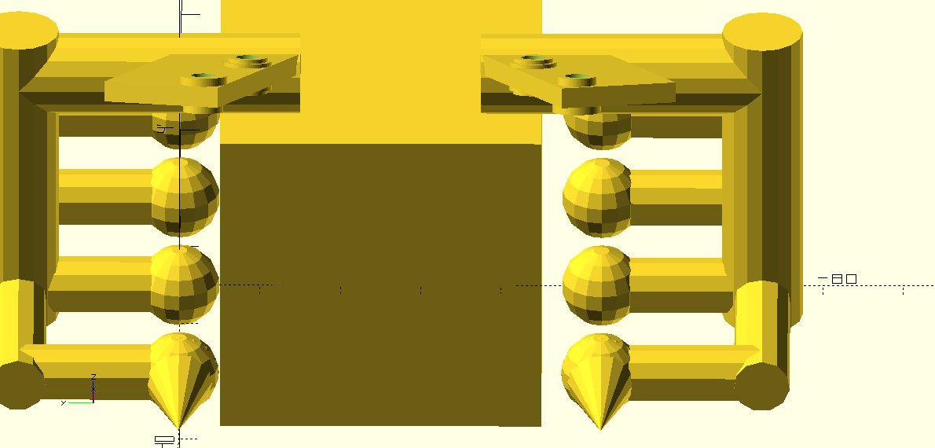
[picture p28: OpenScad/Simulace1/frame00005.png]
 s

# Rozteč 27,0mm
 

# Rozteč 31,5mm
 

# Rozteč 36,0mm
 

# Rozteč 40,5mm


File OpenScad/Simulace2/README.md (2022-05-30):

# Simulace1
Kostka  bude uchycená podélné.
Test podélné manipulace při kostce podélné.
Optika je 2D kvůli názornosti.

# Rozteč 0,0mm
Nereálné stavy.
 

# Rozteč 4,5mm
 

# Rozteč 9,0mm
 

# Rozteč 13,5mm
 

# Rozteč 18,0mm
Od 18mm možná manipulace... (Simulace3)
 

# Rozteč 22,5mm
 

# Rozteč 27,0mm
 

# Rozteč 31,5mm
 

# Rozteč 36,0mm
Pohyb s kostkou na šikmo pro menší rozteč není ideální.
 

# Rozteč 40,5mm


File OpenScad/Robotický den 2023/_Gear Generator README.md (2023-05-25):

# gears.scad

In order to use this code, you will need to copy gears.scad to your Libraries folder.
https://en.wikibooks.org/wiki/OpenSCAD_User_Manual/Libraries

And then you can run *Untitled.scad* as any other normal scad project file.

If you don't want to mess around with the library, just combine the two code files together into one.

## Library Functions

This code will provide a function

**spur_gear()**

Which takes the following parameters:
- N = Number of teeth
- P = Diametral Pitch (defaults to 12)
- pa = Pressure Angle (defaults to 14.5)

The output of this method will be a 2D gear (converted to mm) which you simply need to *linear_extrude* in order to print on a 3D printer.

The library also includes a number of other mathematical functions including:

**calc_center_distance()**

Which takes the following parameters:
- N1 = Tooth count of the first gear
- N2 = Tooth count of the second gear
- P = Diametral Pitch

The output of this function will be the mm distance you must space both gears for them to mesh perfectly.

picture of the openscad output A gear generated with this script

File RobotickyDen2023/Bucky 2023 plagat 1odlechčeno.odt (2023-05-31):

BuckysPlasticArm

Robota BuckysPlasticArm jsem vždy koncipoval jako prostředek k rozvíjený znalostí v oblasti IOT. Robot je řízen přes webové rozhraní v kombinaci s joysticky. Veškerá komunikace je vedena přes webserver umístěný na robotovi v podobě ESP32, který zároveň ovládá celého robota.

Zapojení webserveru má svoje výhody ale i nevýhody. Jednou nespornou výhodou je možnost se podílet více zařízeními na ovládání robota. Navíc se stačí jen připojit do stejné sítě a v prohlížeči zadat ip adresu, kterou ukazuje robot.

Nevýhodou není ani webserver, ale spojení přes wifi, která není stavěná na spojitou komunikaci. To značně komplikuje situaci webserveru.

Nesmím zapomenout na historii robota. Tento robot se jako rychlo projekt zúčastnil minulý rok Robotického dne na disciplíně Toy Cleanup Beginner. Za dobu existence robota už měl tři různé konstrukce, dva různé hardwary a nekonečně uprav v softwaru. Přírůstkem jsou joysticky. Toto zařízení má čtyři joysticky PS4 a signál zpracovává STM32, které posílá data přes mobilní aplikaci, mnou modifikovanou, přes router do robota. Je úplné k nevíře, že řízení pomoci webu a joysticků je v reálném čase.

Více si můžete přečíst na githabu:

https://github.com/PNmJunior/RB2022-TymRECYLKON-TCB-BuckysPlasticArm.git


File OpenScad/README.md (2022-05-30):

# 3D modely
Tohle jsou modely vytvořeno pomoci programu OpenSCAD. https://openscad.org/
## kleste
Je zde navržen tvar kleští pro manipulaci kostek...
### Simulace ...
Soubor obrázku simulujících pohyb ramene vůči kostce
#### Simulace1
Test uchycení podélné kostky.
Test manipulace při kostce podélné.
#### Simulace2
Test manipulace při kostce na šikmo.
#### Simulace3
Test uchycení na šikmo kostky.
### kleste.stl
Je to v poloze vhodné pro 3D tisk. Kvůli nutnosti mýt pevnou a přesně tvarovanou úchytku na pohybující se mechanizmus.

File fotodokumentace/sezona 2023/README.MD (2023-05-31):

# Fotodokumentace

# Soutěžní podoba
31.5.2023




28.5.2023


21.12.2022


10.12.2022



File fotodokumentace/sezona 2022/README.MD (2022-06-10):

# Fotodokumentace

# Soutěžní podoba



## Podoba 3.6.



## Kleště


## Robot


## Původní rameno


## Elektronika uvnitř původního beteryboxu

 
 A navazující problém s objeme kabelů...

 

 ## Popis motorů

 

  ## Podvozek 28.5.2022

 

 Přidaní otočných koulích.



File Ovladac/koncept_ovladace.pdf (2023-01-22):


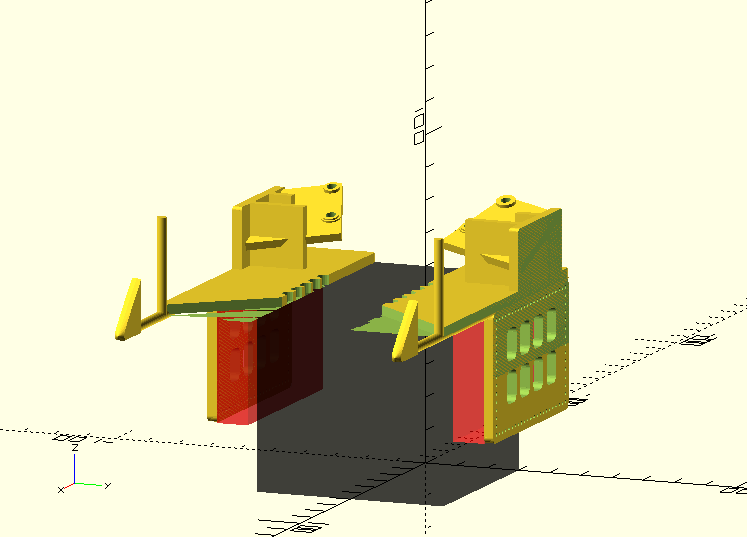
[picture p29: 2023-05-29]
OpenScad/Robotický den 2023/frame00007.png

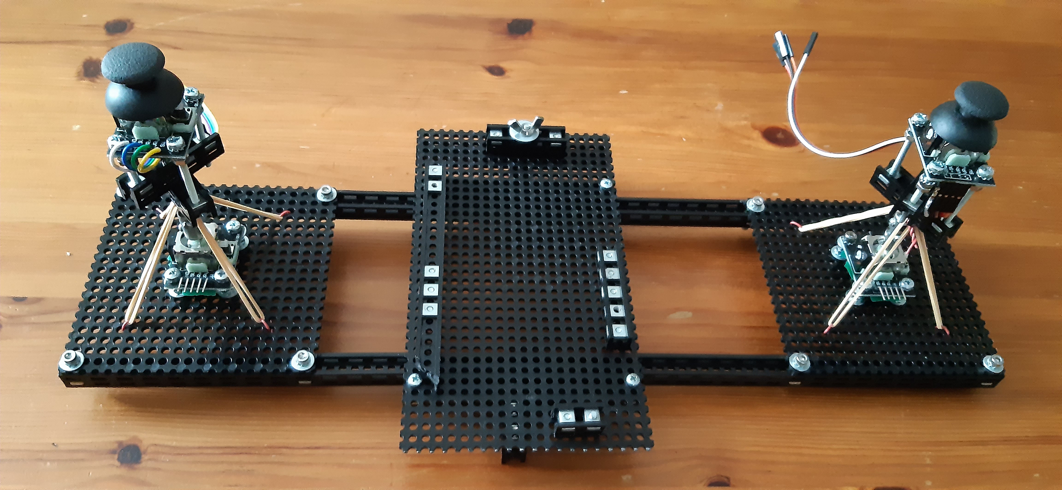
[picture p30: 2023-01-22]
Ovladac/fotky/ovladac_22_1_2023.jpg

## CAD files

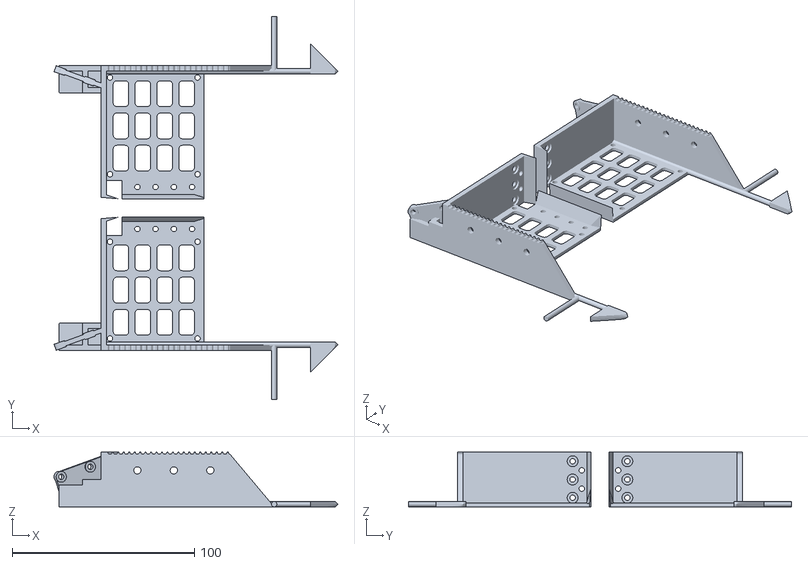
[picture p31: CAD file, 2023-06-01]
OpenScad/Robotický den 2023/kleste1 6 23.stl
155.7 x 210.0 x 30.0

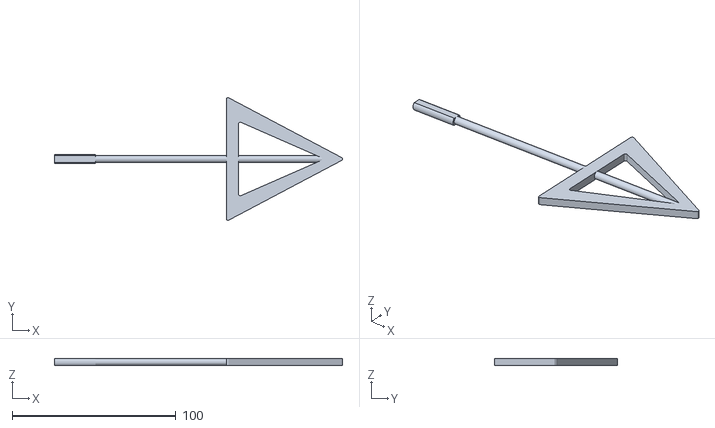
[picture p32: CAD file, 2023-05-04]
OpenScad/Znacka.stl
176.0 x 75.0 x 4.20

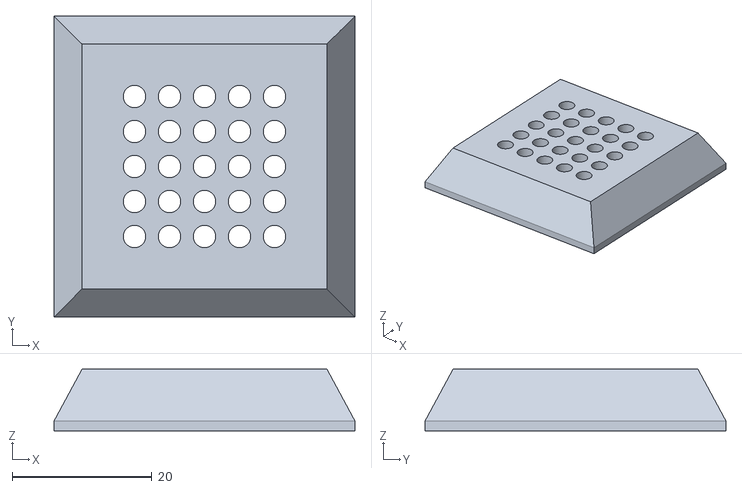
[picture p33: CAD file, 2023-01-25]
Ovladac/Rychloupínák_na_stativ.stl
43.0 x 43.0 x 8.80

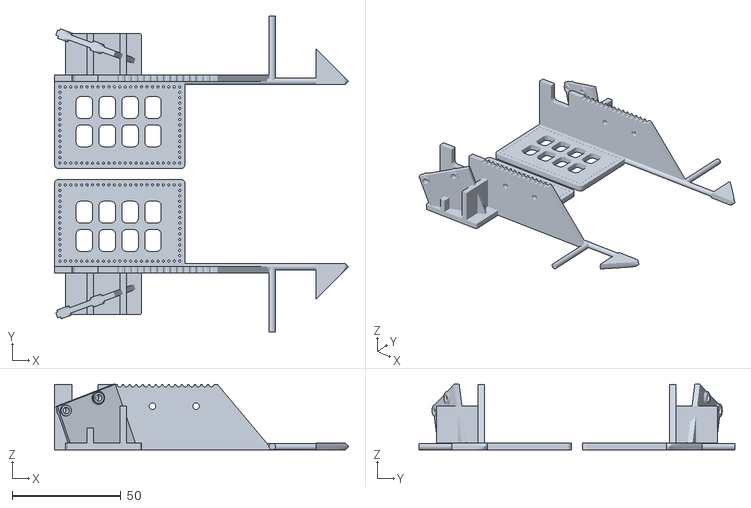
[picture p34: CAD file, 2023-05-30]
OpenScad/Robotický den 2023/klesteOprava31_5_2023.stl
135.0 x 145.0 x 30.1

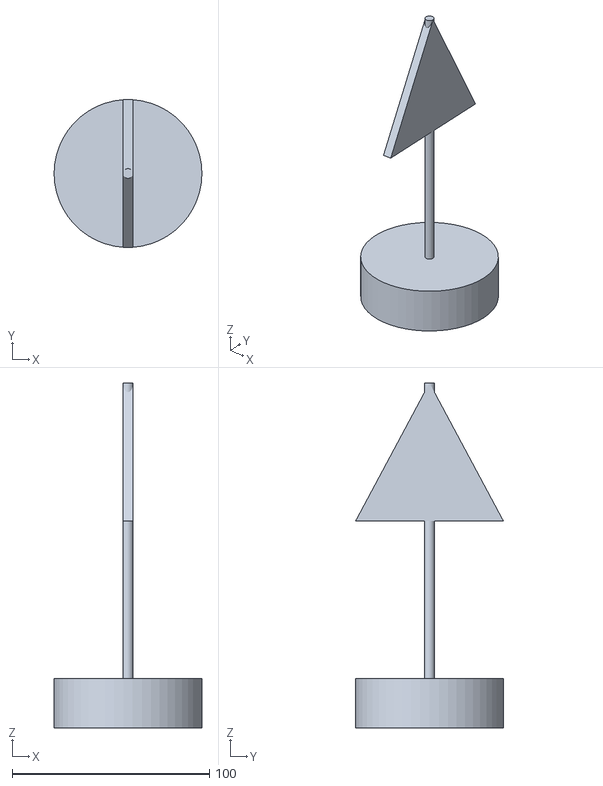
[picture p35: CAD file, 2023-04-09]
OpenScad/ZnackaCela.stl
75.0 x 75.0 x 175.0

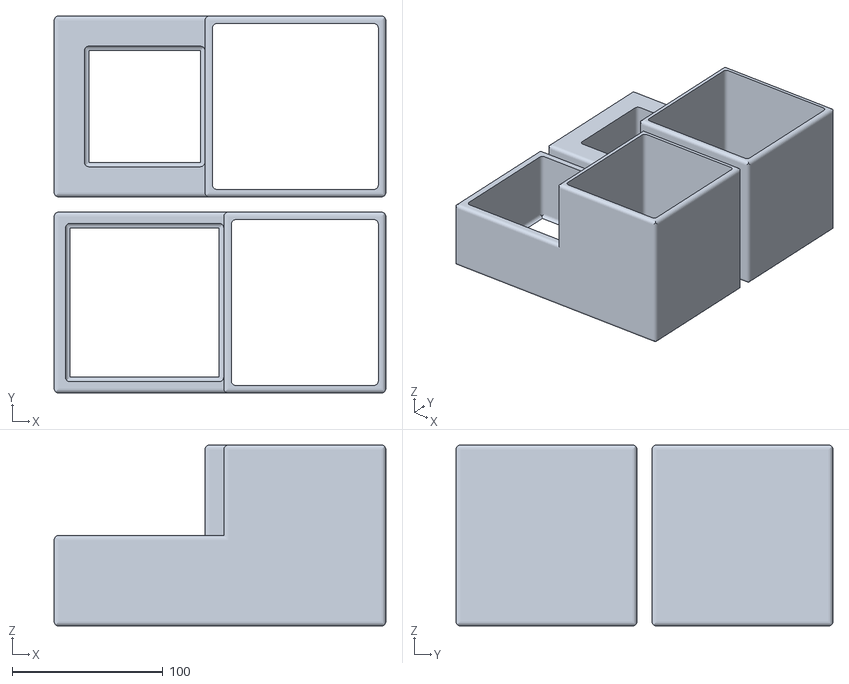
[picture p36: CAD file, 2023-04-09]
OpenScad/Auto.stl
220.0 x 250.0 x 120.0

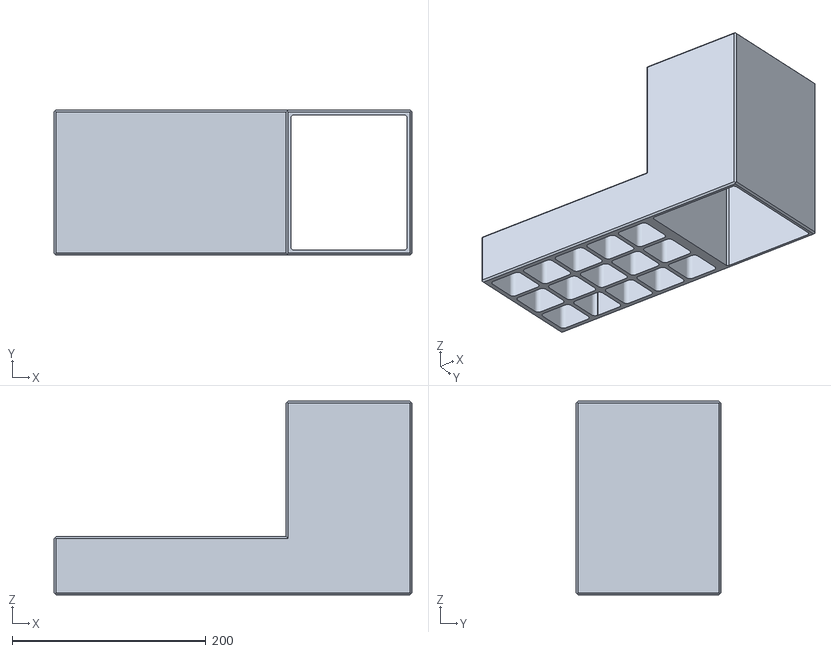
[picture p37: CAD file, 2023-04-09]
OpenScad/NahradniVozidlo.stl
370.0 x 150.0 x 200.0

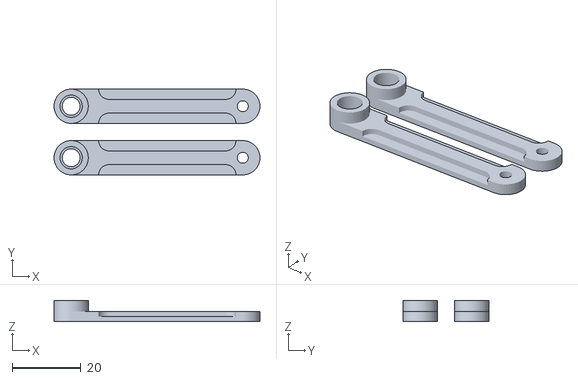
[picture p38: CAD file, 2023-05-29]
OpenScad/Robotický den 2023/tahloOprava.stl
60.0 x 25.0 x 6.20

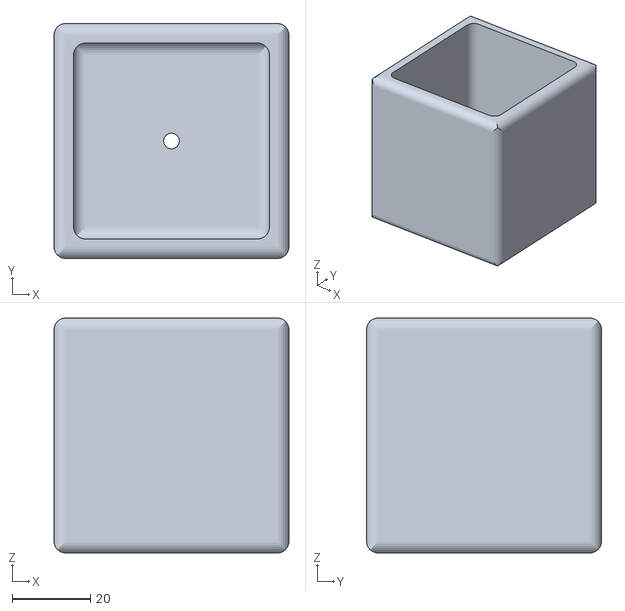
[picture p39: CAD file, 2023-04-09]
OpenScad/BaterieKostky.stl
60.0 x 60.0 x 60.0

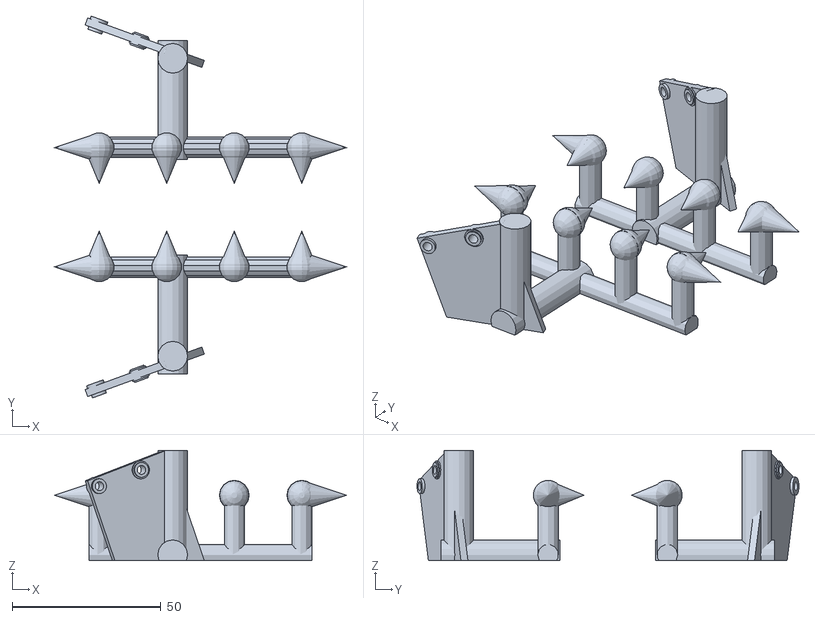
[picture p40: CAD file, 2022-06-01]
OpenScad/kleste5.stl
98.0 x 128.2 x 37.1

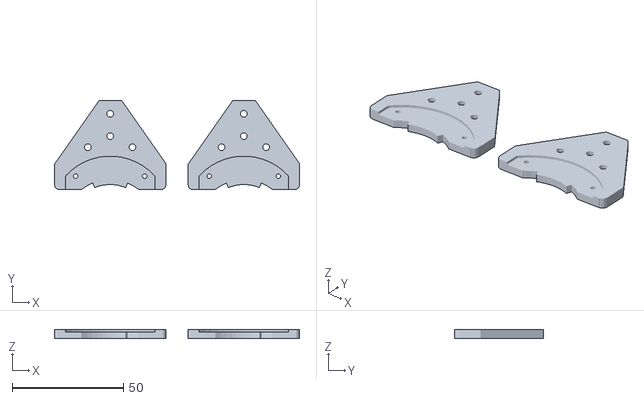
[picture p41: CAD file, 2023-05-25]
OpenScad/Robotický den 2023/NosnikB.stl
110.0 x 40.0 x 4.00

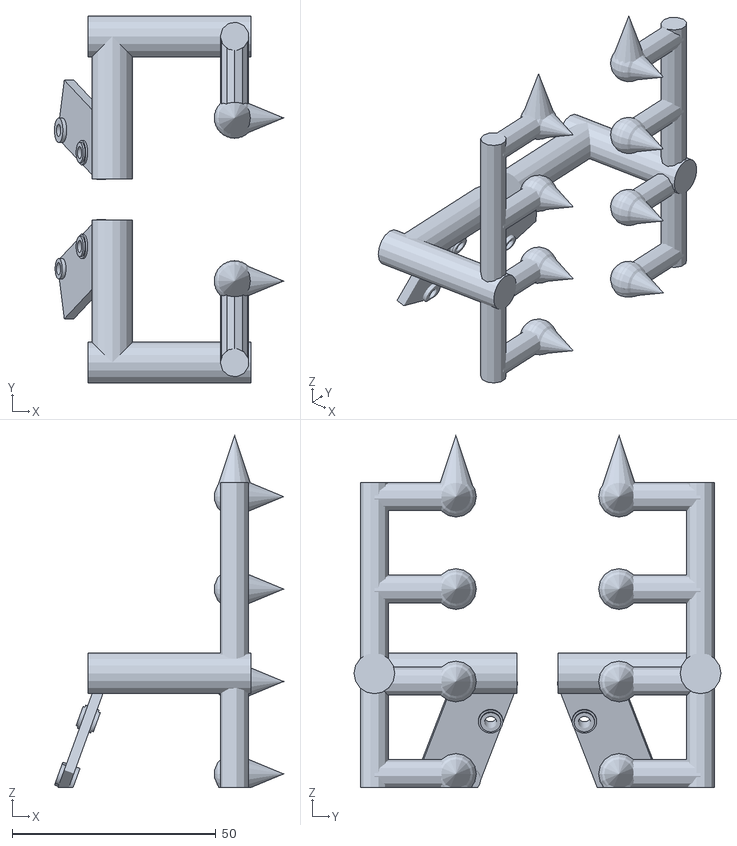
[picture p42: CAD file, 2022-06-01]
OpenScad/kleste4.stl
56.2 x 90.0 x 86.3

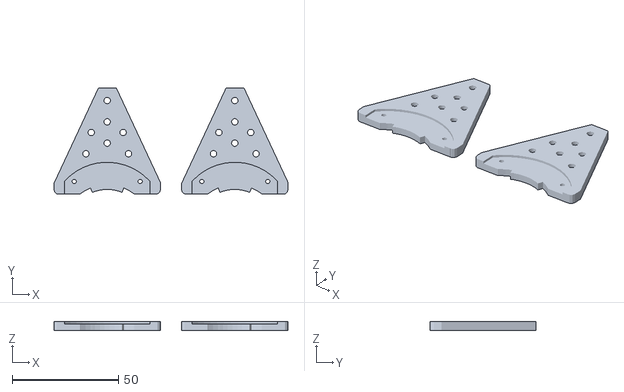
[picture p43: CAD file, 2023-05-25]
OpenScad/Robotický den 2023/NosnikA.stl
110.0 x 50.0 x 4.00

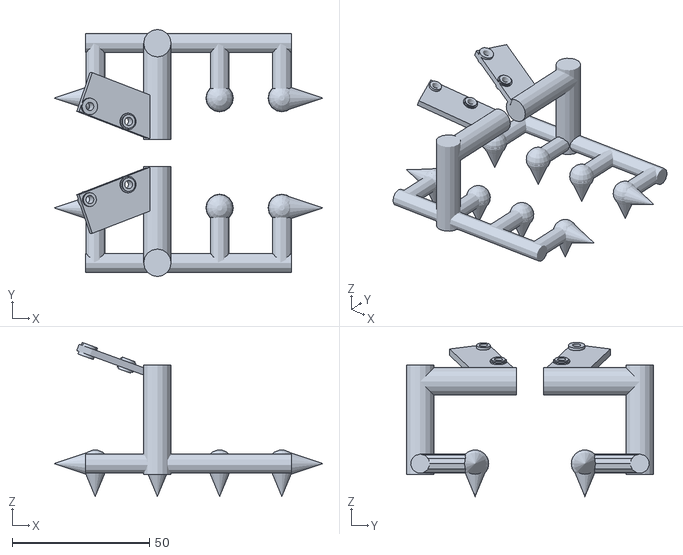
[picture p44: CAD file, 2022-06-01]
OpenScad/kleste2.stl
98.0 x 90.0 x 56.2

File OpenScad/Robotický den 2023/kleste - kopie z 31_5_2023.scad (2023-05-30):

pena = 10;
vrstva = 3;
rameno = 23;
kostka = 60;
alfa=15;

$fn=30;
//tiskBool = false;
tiskBool = true;

//Kleste();
//Redukce();

//KlestePrava();
//Simul();

//Print4();

//Print5();


module tisk()
{
    
    translate([0,45,0]) rotate([-90,0,0]) KlesteLeva();
    translate([0,0,0]) rotate([90,0,0]) KlestePrava(); 
    
}
tisk();

module Print4()
{
    difference()
    {
    translate([0,0,00]) rotate([0,270,0]) 
    {
 KlesteLeva();
translate([0,-40,0]) KlestePrava(); 
    } 
    translate([-50,-70,-128]) cube(100);
    } 
}


module Print5()
{
    difference()
    {
    translate([0,0,22]) rotate([0,0,0])
    {
        translate([0,0,0]) rotate([-90,0,0]) KlesteLeva();
        translate([0,-40,0]) rotate([90,0,0]) KlestePrava(); 
    } 
   translate([-100,-100,-200]) cube(200); 
}
}

//Print2();


module Print2()
{
    translate([0,0,0]) rotate([0,0,0])
    {
        KlesteLeva();
        translate([0,-40,0]) KlestePrava(); 
    }  
}


//Print();


module Print()
{
    translate([0,0,35]) rotate([0,160,0])
    {
        KlesteLeva();
        translate([0,-40,0]) KlestePrava(); 
    }  
}


module Simul()
{
    //i = 0;
    i = $t;
    kk = alfa+i*rameno;
    translate([0,kk,40]) KlesteLeva();
    //translate([0,-30-$t*2*rameno,0]) KlestePrava();  
   translate([0,-kk,40]) KlestePrava();   
    //translate([11,-52,-20])rotate([0,0,45])  cube(40);
    //translate([23,-62,-20])rotate([0,0,45])  cube(40);
    translate([0,-kostka/2,0]) color("black",0.5) cube(kostka);    
}

posun = 30;
module KlesteLeva()
{   difference()
   { 
    translate([0,0,0])
        {
        translate([-28+posun,-2,42]) rotate([0,20,0])
            { 
                rotate([0,0,-20]) Redukce();

            }
            mirror([0,1,0])translate([0,0,0]) Kleste();
            
        }
        translate([0,alfa ,0]) cube(100);
    }
}


module KlestePrava()
{    
    difference()
    {
        translate([0,0,0])
        {
            translate([-28+posun,2,42]) rotate([0,20,0])
            {
                rotate([180,0,20]) Redukce();
            }
            translate([0,0,0]) Kleste(); 
        }   
        translate([0,-alfa-100 ,0]) cube(100);
    }
}


module plocha(rozd)
{
    mezera = 2.5;
    odx = 10;
    odxS = (rozd[0]-odx*3)/4;
    odxSO = odxS + 3;
    odz = 10;
    odzS = 10;
    odzSO = odzS + 3;
    difference()
    {
        OvalnaKrichleY(rozd,2);
        //pro osu y
        for(x = [mezera:mezera:rozd[0] - mezera])
        {
            translate([x,rozd[1]*2,rozd[2]-mezera]) rotate([90,0,0]) cylinder(h = 100,d = 1);
            translate([x,rozd[1]*2,mezera]) rotate([90,0,0]) cylinder(h = 100,d = 1);
        }
        for(z = [mezera:mezera:rozd[2] - mezera])
        {
            translate([rozd[0]-mezera,rozd[1]*2,z]) rotate([90,0,0]) cylinder(h = 100,d = 1);
            translate([mezera,rozd[1]*2,z]) rotate([90,0,0]) cylinder(h = 100,d = 1);
        }
        
        for(x = [odx:odxSO:rozd[0] - odx])
        {
            for(z = [odz:odzSO:rozd[2] - odz])
            {
                translate([x,-10,z]) OvalnaKrichleY([odxS,100, odzS],2);
                
            }
            
        }
    }
    
    
}

module Kleste()
{

    v = pena + vrstva;
    vyskaCenter = 20;
    vyskaPlochy = 40;
    sirkaPlochy = 60;
    rezer = 10;
    odstup = sirkaPlochy + 40;

    //translate([j+j+bb/2-2,-v,0]) rotate([0,-90,0]) cylinder(h=bb+3*j,d=bb,center = false);

    
    //translate([0,-v,-4])  cylinder(h=40,d=10,center = false);
    translate([0,alfa,0]) 
    {
        //rotate([90,0,0]) cylinder(h=alfa+v,d=10,center = false);
        translate([0,-(kostka/2-rameno + pena+ vrstva + rezer),0]) {
            translate([0,0,vyskaCenter-vyskaPlochy])
            {
            
                plocha([sirkaPlochy ,vrstva,vyskaPlochy]);
                if(tiskBool == false)
                {
                    
                    translate([0,+ vrstva,0]) color("red",0.5) cube([sirkaPlochy ,pena,vyskaPlochy]);
                }
            }
            translate([0,0,vyskaCenter])
            {
                translate([0,vrstva/2,0]) rotate([0,90,0]) cylinder(h = odstup,d = vrstva);
                translate([odstup, vrstva/2,0 ]) 
                {
                   translate([0,0,0]) cylinder(h = 30,d = vrstva);
                   translate([0,0,0]) rotate([0,90,0]) cylinder(h = 20,d = vrstva);
                    translate([20,0,0]) intersection()
                    {
                        delkaPredHaku = 15;
                        vyskaPredHaku = 15;
                        rotate([0,90,0]) cylinder(h = delkaPredHaku, r1 = vyskaPredHaku, r2=0);
                        translate([0,-vrstva/2,-vrstva/2])cube([delkaPredHaku, vrstva, vyskaPredHaku + vrstva]);
                    }
                }
                vyskaPPP = 22;
               translate([posun -25,0,0]) OvalnaKrichleY([35,vrstva, vyskaPPP]); 
                translate([posun -15,0,0]) cube([vrstva, 10,vyskaPPP]);
                translate([posun ,0,0]) cube([vrstva, 20,vyskaPPP]);
                difference()
                {
                translate([0,0,0])cube([odstup,kostka/2-rameno + pena+ vrstva + rezer, vrstva]);
                    translate([odstup,0,0]) rotate([0,0,40]) cube(100);
                    translate([8,20,00]) rotate([0,0,00])  OvalnaKrichleZ([12,12,12],2);
                    for(x = [30:3:74])
                    {
                        translate([x,kostka/2-rameno + pena+ vrstva + rezer,0]) cylinder(h = 100, d = 2.3);
                        
                    }
                    translate([45,kostka/2-rameno + pena+ vrstva + rezer-10,0]) cylinder(h = 100, d = 3);
                    translate([65,kostka/2-rameno + pena+ vrstva + rezer-10,0]) cylinder(h = 100, d = 3);
                }
            }
            
        }
        
        
    }
}


module Redukce()
{
    translate([0,0,-2.5/2]) difference()
    {
        union()
        {
            translate([3,0,0]) cylinder(h=2.5+1,d=6,center=false,$fn=64);
            translate([3,0,-1]) cylinder(h=1,d=5,center=false,$fn=64);   
            translate([0,-3,0]) cube([30,40,2.5]);
            translate([20,0,-0.5]) cylinder(h=3.5,d=6,center=false,$fn=64);
            translate([20,0,-1]) cylinder(h=4.5,d=5,center=false,$fn=64);
        }
        translate([3,0,-1.5]) cylinder(h=10,d=3,center=false,$fn=64);
        translate([20,0,-1.5]) cylinder(h=10,d=3,center=false,$fn=64);   
    }
}



//Kód pro vytvoření oválných kvádrů
module OvalnaKrichleX(Rozdmery, zakulaceni = 1,st = 30)
{
	union() {
	translate([0,zakulaceni,0]) cube([Rozdmery[0],Rozdmery[1] - zakulaceni * 2,Rozdmery[2]],center=false);
	translate([0,0,zakulaceni]) cube([Rozdmery[0],Rozdmery[1],Rozdmery[2] - zakulaceni * 2],center=false);
	translate([0,zakulaceni,zakulaceni]) rotate([0,90,0]) cylinder( Rozdmery[0],   zakulaceni, zakulaceni,false,$fn=st);
	translate([0,Rozdmery[1] - zakulaceni,zakulaceni]) rotate([0,90,0]) cylinder( Rozdmery[0],   zakulaceni, zakulaceni,false,$fn=st);
	translate([0,zakulaceni,Rozdmery[2] - zakulaceni]) rotate([0,90,0]) cylinder( Rozdmery[0],   zakulaceni, zakulaceni,false,$fn=st);
	translate([0,Rozdmery[1] - zakulaceni,Rozdmery[2] - zakulaceni]) rotate([0,90,0]) cylinder( Rozdmery[0],   zakulaceni, zakulaceni,false,$fn=st);
	}
}


module OvalnaKrichleY(Rozdmery, zakulaceni = 1,st = 30)
{
	union() {
	translate([zakulaceni,0,0]) cube([Rozdmery[0] - zakulaceni * 2,Rozdmery[1],Rozdmery[2]],center=false);
	translate([0,0,zakulaceni]) cube([Rozdmery[0],Rozdmery[1],Rozdmery[2] - zakulaceni * 2],center=false);
	translate([zakulaceni,0,zakulaceni]) rotate([270,0,0]) cylinder( Rozdmery[1],   zakulaceni, zakulaceni,false,$fn=st);
	translate([Rozdmery[0] - zakulaceni,0,zakulaceni]) rotate([270,0,0]) cylinder( Rozdmery[1],   zakulaceni, zakulaceni,false,$fn=st);
	translate([zakulaceni,0,Rozdmery[2] - zakulaceni]) rotate([270,0,0]) cylinder( Rozdmery[1],   zakulaceni, zakulaceni,false,$fn=st);
	translate([Rozdmery[0] - zakulaceni,0,Rozdmery[2] - zakulaceni]) rotate([270,0,0]) cylinder( Rozdmery[1],   zakulaceni, zakulaceni,false,$fn=st);
	}
}


module OvalnaKrichleZ(Rozdmery, zakulaceni = 1,st = 30)
{
	union() {
	translate([zakulaceni,0,0]) cube([Rozdmery[0] - zakulaceni * 2,Rozdmery[1],Rozdmery[2]],center=false);
	translate([0,zakulaceni,0]) cube([Rozdmery[0],Rozdmery[1]  - zakulaceni * 2,Rozdmery[2]],center=false);
	translate([zakulaceni,zakulaceni,0]) rotate([0,0,0]) cylinder( Rozdmery[2],   zakulaceni, zakulaceni,false,$fn=st);
	translate([Rozdmery[0] - zakulaceni,zakulaceni,0]) rotate([0,0,0]) cylinder( Rozdmery[2],   zakulaceni, zakulaceni,false,$fn=st);
	translate([zakulaceni,Rozdmery[1] - zakulaceni,0]) rotate([0,0,0]) cylinder( Rozdmery[2],   zakulaceni, zakulaceni,false,$fn=st);
	translate([Rozdmery[0] - zakulaceni,Rozdmery[1] - zakulaceni,0]) rotate([0,0,0]) cylinder( Rozdmery[2],   zakulaceni, zakulaceni,false,$fn=st);
	}
}
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

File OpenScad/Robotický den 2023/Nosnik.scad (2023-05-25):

module pieSlice(a, r, h){
  // a:angle, r:radius, h:height
  rotate_extrude(angle=a) square([r,h]);
}
//pieSlice(110,20,3);

    motorKul = 54;//53.8
    motorVyska = 40.2;//40.1
    motorSirka  = 29.3;
    motorDiraVel = 2;
    motorDiraY = 36;
    motorDiraX = 31;
    motorVM = 25.4;
    motorVV = 33.6;
    motorVS = 5.2;
    motorVelkeUhel = 45;
    motorVelke = 41;//40.5
    motorMale = 36.5;//36.1
    motorAsimetrie = (motorVV - motorVS/2)-motorKul/2;
$fn=50;

module motor()
{

    echo(motorAsimetrie);
    $fn=50;
    
    rotate([0,0,180]) translate([-motorVyska/2,-motorAsimetrie,]) 
    {
        difference()
        {
            cylinder(motorSirka, d = motorKul, $fn=50);
            translate([-(motorVyska/2+40),-motorKul/2,0]) cube([40,motorKul,motorSirka]);
            translate([motorVyska/2,-motorKul/2,0]) cube([40,motorKul,motorSirka]);
            
        }
        translate([-motorDiraX/2, - motorDiraY/2,-50 + motorSirka/2])
        {
            translate([0,0,0]) cylinder(h = 100, d = motorDiraVel, $fn=50);
            translate([motorDiraX,0,0]) cylinder(h = 100, d = motorDiraVel, $fn=50);
            translate([0,motorDiraY,0]) cylinder(h = 100, d = motorDiraVel, $fn=50);
            translate([motorDiraX,motorDiraY,0]) cylinder(h = 100, d = motorDiraVel, $fn=50);
        }
        translate([0,motorAsimetrie,-50 + motorSirka/2])
        {
            cylinder(h = 100, d = motorMale, $fn=50);
            rotate([0,0,-90 + motorVelkeUhel/2]) pieSlice(180-motorVelkeUhel, motorVelke/2, 100);
            rotate([0,0,180-90 + motorVelkeUhel/2]) pieSlice(180-motorVelkeUhel, motorVelke/2, 100);
        }
        
    }
    
}

//motor();

module troj()
{
    translate([-40,30,0]) rotate([0,0,-25]) cube([40,100,30]);
    
    
}




module nosnik()
{
    vyska = 4;
    vyskaVyrez = 3;
    difference()
    {
        translate([0,0,0])
        {
            translate([0,16,0]) OvalnaKrichleZ([50,50,4],2);
            
            
        }
        translate([(50-motorVyska)/2,0,vyskaVyrez]) motor();
        translate([0,0,-10])
        {
            translate([25,40,0]) cylinder(h = 20, d = 3);
            translate([25,50,0]) cylinder(h = 20, d = 3);
            translate([25,60,0]) cylinder(h = 20, d = 3);
            translate([15,35,0]) cylinder(h = 20, d = 3);
            translate([35,35,0]) cylinder(h = 20, d = 3);
            translate([17.5,45,0]) cylinder(h = 20, d = 3);
            translate([32.5,45,0]) cylinder(h = 20, d = 3);
        }
        
        translate([0,0,-10])
        {
            troj();
            mirror([1,0,0]) translate([-motorVyska-10,0,0]) troj();
        }   
    }
}

translate([0,0,0]) nosnik();
translate([60,0,0]) nosnik();

//Kód pro vytvoření oválných kvádrů
module OvalnaKrichleX(Rozdmery, zakulaceni,st = 10)
{
	union() {
	translate([0,zakulaceni,0]) cube([Rozdmery[0],Rozdmery[1] - zakulaceni * 2,Rozdmery[2]],center=false);
	translate([0,0,zakulaceni]) cube([Rozdmery[0],Rozdmery[1],Rozdmery[2] - zakulaceni * 2],center=false);
	translate([0,zakulaceni,zakulaceni]) rotate([0,90,0]) cylinder( Rozdmery[0],   zakulaceni, zakulaceni,false,$fn=st);
	translate([0,Rozdmery[1] - zakulaceni,zakulaceni]) rotate([0,90,0]) cylinder( Rozdmery[0],   zakulaceni, zakulaceni,false,$fn=st);
	translate([0,zakulaceni,Rozdmery[2] - zakulaceni]) rotate([0,90,0]) cylinder( Rozdmery[0],   zakulaceni, zakulaceni,false,$fn=st);
	translate([0,Rozdmery[1] - zakulaceni,Rozdmery[2] - zakulaceni]) rotate([0,90,0]) cylinder( Rozdmery[0],   zakulaceni, zakulaceni,false,$fn=st);
	}
}


module OvalnaKrichleY(Rozdmery, zakulaceni,st = 10)
{
	union() {
	translate([zakulaceni,0,0]) cube([Rozdmery[0] - zakulaceni * 2,Rozdmery[1],Rozdmery[2]],center=false);
	translate([0,0,zakulaceni]) cube([Rozdmery[0],Rozdmery[1],Rozdmery[2] - zakulaceni * 2],center=false);
	translate([zakulaceni,0,zakulaceni]) rotate([270,0,0]) cylinder( Rozdmery[1],   zakulaceni, zakulaceni,false,$fn=st);
	translate([Rozdmery[0] - zakulaceni,0,zakulaceni]) rotate([270,0,0]) cylinder( Rozdmery[1],   zakulaceni, zakulaceni,false,$fn=st);
	translate([zakulaceni,0,Rozdmery[2] - zakulaceni]) rotate([270,0,0]) cylinder( Rozdmery[1],   zakulaceni, zakulaceni,false,$fn=st);
	translate([Rozdmery[0] - zakulaceni,0,Rozdmery[2] - zakulaceni]) rotate([270,0,0]) cylinder( Rozdmery[1],   zakulaceni, zakulaceni,false,$fn=st);
	}
}


module OvalnaKrichleZ(Rozdmery, zakulaceni,st = 10)
{
	union() {
	translate([zakulaceni,0,0]) cube([Rozdmery[0] - zakulaceni * 2,Rozdmery[1],Rozdmery[2]],center=false);
	translate([0,zakulaceni,0]) cube([Rozdmery[0],Rozdmery[1]  - zakulaceni * 2,Rozdmery[2]],center=false);
	translate([zakulaceni,zakulaceni,0]) rotate([0,0,0]) cylinder( Rozdmery[2],   zakulaceni, zakulaceni,false,$fn=st);
	translate([Rozdmery[0] - zakulaceni,zakulaceni,0]) rotate([0,0,0]) cylinder( Rozdmery[2],   zakulaceni, zakulaceni,false,$fn=st);
	translate([zakulaceni,Rozdmery[1] - zakulaceni,0]) rotate([0,0,0]) cylinder( Rozdmery[2],   zakulaceni, zakulaceni,false,$fn=st);
	translate([Rozdmery[0] - zakulaceni,Rozdmery[1] - zakulaceni,0]) rotate([0,0,0]) cylinder( Rozdmery[2],   zakulaceni, zakulaceni,false,$fn=st);
	}
}


module OvalnaKrichle(Rozdmery, zakulaceni, osaX, osaY, osaZ, st = 10)
{
	cont = false;
	intersection()
	{
		if(osaX == true)
		{
			OvalnaKrichleX(Rozdmery,zakulaceni,st);
			cont = true;
		}
		if(osaY == true)
		{
			OvalnaKrichleY(Rozdmery,zakulaceni,st);
			cont = true;
		}
		if(osaZ == true)
		{
			OvalnaKrichleZ(Rozdmery,zakulaceni,st);
			cont = true;
		}
		if(cont == false)
		{
			cube(Rozdmery,center=false);
		}
	}
}


module OvalnaKrichleCisla(Rozdmery, osaX, osaY, osaZ ,st = 10 )
{
	cont = false;
	intersection()
	{
		if(osaX != 0)
		{
			OvalnaKrichleX(Rozdmery,osaX,st);
			cont = true;
		}
		if(osaY != 0)
		{
			OvalnaKrichleY(Rozdmery,osaY,st);
			cont = true;
		}
		if(osaZ != 0)
		{
			OvalnaKrichleZ(Rozdmery,osaZ,st);
			cont = true;
		}
		if(cont == false)
		{
			cube(Rozdmery,center=false);
		}
	}
}

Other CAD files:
OpenScad/Robotický den 2023/kleste31_5_2023.stl
OpenScad/Robotický den 2023/tahlo.stl
OpenScad/Robotický den 2023/Prevodniky tisk.stl
OpenScad/kleste3.stl
OpenScad/Robotický den 2023/kleste.scad
OpenScad/Robotický den 2023/NosnikB.scad
OpenScad/Auto.scad
OpenScad/BaterieKostky.scad
OpenScad/Engrenage.stl
OpenScad/NahradniVozidlo.scad
OpenScad/Robotický den 2023/Prevodniky text.stl
OpenScad/Robotický den 2023/Prevodniky.scad
OpenScad/Robotický den 2023/gear-generation-example.scad
OpenScad/Robotický den 2023/gears.scad
OpenScad/Robotický den 2023/tahlo.scad
OpenScad/Znacka.scad
OpenScad/chapadlo2023.scad
OpenScad/kleste.stl
Ovladac/Rychloupínák_na_stativ.scad

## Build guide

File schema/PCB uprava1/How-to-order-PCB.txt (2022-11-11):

How to Order PCB

Please refer to:
https://docs.easyeda.com/en/PCB/Order-PCB

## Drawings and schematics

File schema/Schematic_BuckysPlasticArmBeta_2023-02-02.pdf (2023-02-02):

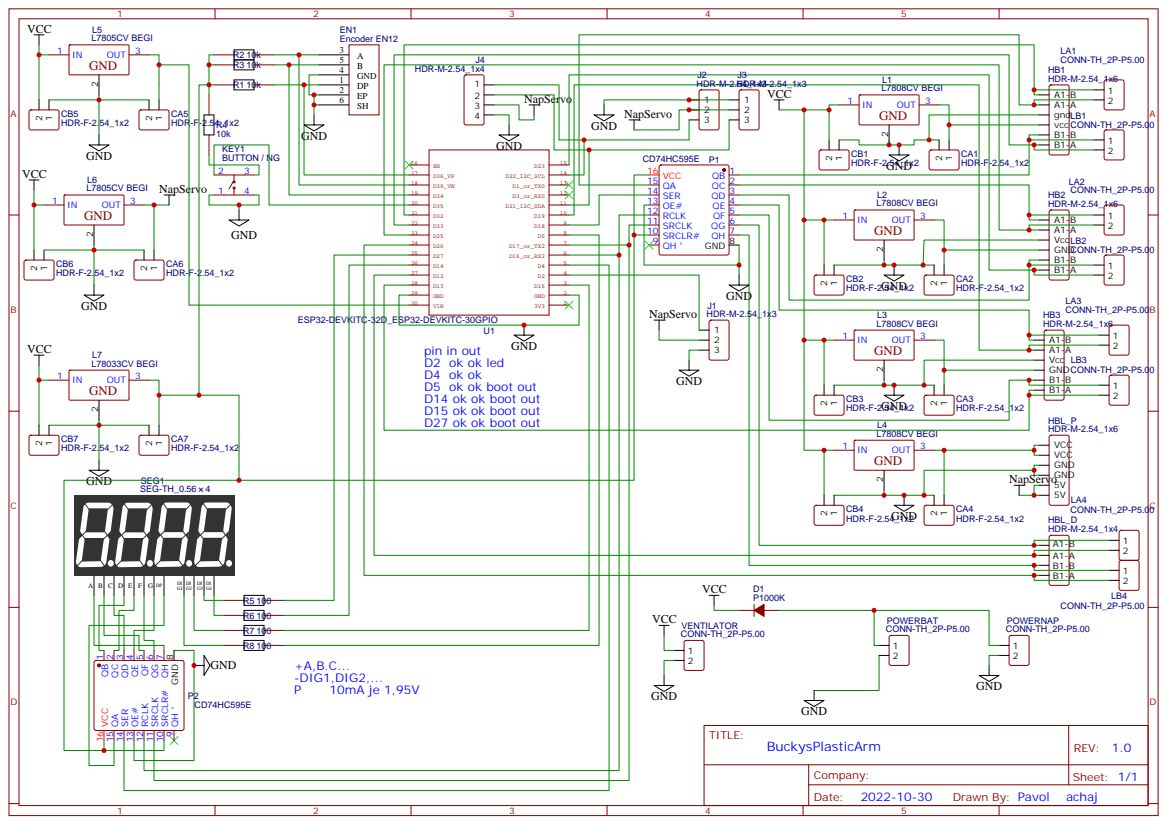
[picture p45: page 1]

HDR-M-2.54_1x4 1 | J2 J3 L1

L7808CV BEGI VCC

SRCLR# 10 SRCLK 11 RCLK 12 OE# 13 SER 14 QA 15 VCC 16

pin in out
D2 ok ok led
D5 ok ok boot out
D14 ok ok boot out
D15 ok ok boot out
D27 ok ok boot out

9 SRCLR# 10 SRCLK 11 RCLK 12 OE# 13 SER 14 QA 15 VCC 16

Drawn By: Pavol achaj

# CAx CBx

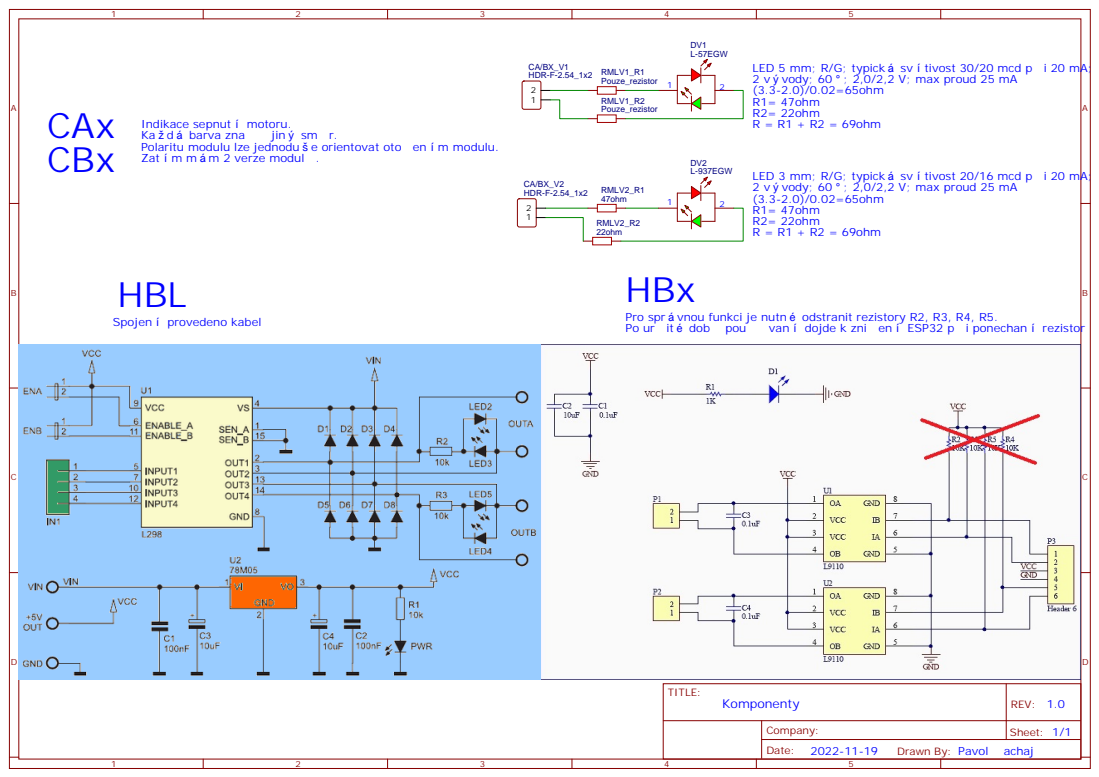
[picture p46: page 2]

Indikace sepnut motoru.
Ka d barva znaპ퀀 jin sm r.
Polaritu modulu lze jednodu e orientovat oto en m modulu.
Zat m m m 2 verze modul .

LED 3 mm; R/G; typick sv tivost 20/16 mcd p i 20 mA;
2 v vody; 60 ; 2,0/2,2 V; max proud 25 mA
(3.3-2.0)/0.02=65ohm
R1= 47ohm
R2= 22ohm

Pro spr vnou funkci je nutn odstranit rezistory R2, R3, R4, R5.
Po ur it dob pou៮퀀van dojde k zni en ESP32 p i ponechan rezistor

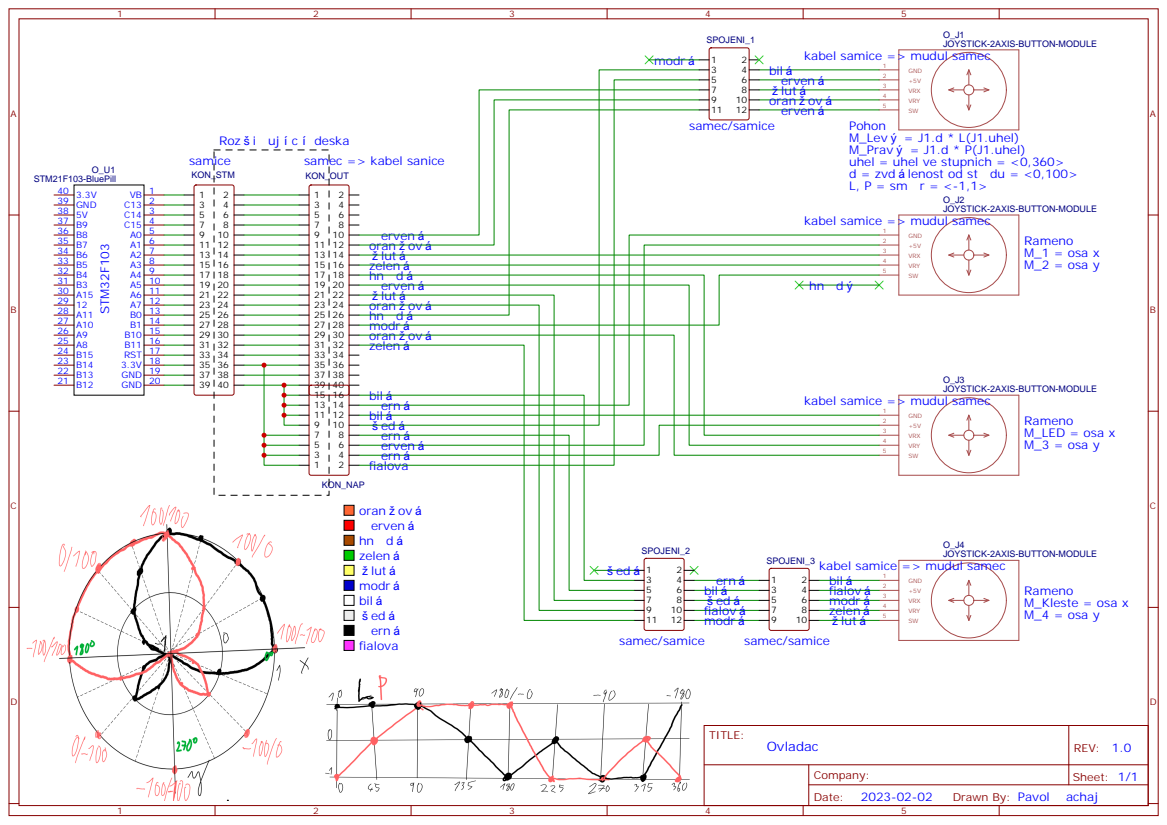
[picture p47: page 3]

kabel samice => mudul samec

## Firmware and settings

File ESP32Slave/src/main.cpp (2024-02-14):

#include <Arduino.h>
#include <WiFi.h>
#include <AsyncTCP.h>
#include <ESPAsyncWebServer.h>
#include <AsyncElegantOTA.h>
#include <disp.h>
#include <motor.h>
#include <komunProtokol.h>
#include <enkoder.h>
#include <menu.h>
#include "SPIFFS.h"      //nastaveni webu
#include <Preferences.h> //Ulozeni hesla
#include <consol.h>

consol cons;

Preferences preferences;

String WifiNotPassword = "@";

// nove definice
#define pin_PR_Clock 17
#define pin_PR_Data1 18
#define pin_PR_Data2 4
#define pin_PR_Latch 16
#define pin_Servo2 22
#define pin_Servo3 23
#define pin_Servo1 2
#define pin_m0 32
#define pin_m1 33
#define pin_m2 25
#define pin_m3 23
#define pin_m4 19
#define pin_m5 13
#define pin_m6 12
#define pin_m7 26
#define pin_LedD1 5
#define pin_LedD2 15
#define pin_LedD3 27
#define pin_LedD4 14
#define pin_Tlac 35
#define pin_EnkA 39
#define pin_EnkB 34
#define pin_EnkDP 36


#define M_LED 0//0
#define M_1 1//5
#define M_2 2//4
#define M_3 3//3
#define M_4 4//2
#define M_Kleste 5//1
#define M_Levy 6//6
#define M_Pravy 7//7

const byte Prevodnik[8] = {0,5,4,3,2,1,6,7};

const byte NastMotPin[8]= {32,33,25,23,19,13,12,26};//system

const ledc_channel_t NastMotLEDC_CHANNEL[8]= {
  LEDC_CHANNEL_0,//pin 32
  LEDC_CHANNEL_1,//pin 33
  LEDC_CHANNEL_2,//pin 25
  LEDC_CHANNEL_3,//pin 23
  LEDC_CHANNEL_4,//pin 19
  LEDC_CHANNEL_5,//pin 13
  LEDC_CHANNEL_6,//pin 12
  LEDC_CHANNEL_7 //pin 26
};//system

const bool NastMotInverz[8] = {
  false,//pin 32
  false,//pin 33
  false,//pin 25
  false,//pin 23
  false,//pin 19
  false,//pin 13
  false,//pin 12
  false //pin 26
};//realne zapojení na konektoru, razeno postupne

const bool NastMotNeg[8] = {
  false,//M_LED
  false,//M_1
  false,//M_2
  false,//M_3
  false,//M_4
  false,//M_Kleste
  false,//M_Levy
  false //M_Pravy
};//nutnost zmenit smer, razeno podle prevodniku

const byte NastMotMaxMin[8][2] = {
  {255,0},//M_LED
  {190,60},//M_1
  {255,115},//M_2
  {255,80},//M_3
  {255,55},//M_4
  {170,130},//M_Kleste
  {225,110},//M_Levy
  {200,100} //M_Pravy
};//razeno podle prevodniku


disp segDisp;
motor mot;
// komun kom;
hw_timer_t *My_timer = NULL;
//enkoder enk;

byte posunIP = 0;

byte pocetClientu = 0 ;

void IRAM_ATTR HlavniPreruseni()
{
  if(!mot.work)
  {
    mot.work = true;
  byte d1 = mot.vystup();
  //Serial.println(d1);
  //byte d2 = B10000001;
  byte d2 = segDisp.vystup();
  //Serial.println(d2,2);
  byte d3 = segDisp.index();

  digitalWrite(pin_PR_Latch, LOW);
  //delayMicroseconds(10);
  for (uint8_t i = 0; i < 8; i++)//7 - i
  {
    if ((d1>>i)&1)
    {
      digitalWrite(pin_PR_Data1, 1);
    }
    else
    {
      digitalWrite(pin_PR_Data1, 0);
    }
    if ((d2>>i)&1)
    {
      digitalWrite(pin_PR_Data2, 1);     
    }
    else
    {
      digitalWrite(pin_PR_Data2, 0);
    }
    
    //delayMicroseconds(10);
    digitalWrite(pin_PR_Clock, HIGH);
    //delayMicroseconds(10);
    mot.setPWM(i);
    digitalWrite(pin_PR_Clock, LOW);
    //delayMicroseconds(10);
  }

  mot.updatePWM();

  switch (d3)
  {
  case 0:
    digitalWrite(pin_LedD4, 1);
    digitalWrite(pin_LedD1, 0);
    break;
  case 1:
    digitalWrite(pin_LedD1, 1);
    digitalWrite(pin_LedD2, 0);
    break;
  case 2:
    digitalWrite(pin_LedD2, 1);
    digitalWrite(pin_LedD3, 0);
    break;
  case 3:
    digitalWrite(pin_LedD3, 1);
    digitalWrite(pin_LedD4, 0);
    break;

  default:
    digitalWrite(pin_LedD1, 1);
    digitalWrite(pin_LedD2, 1);
    digitalWrite(pin_LedD3, 1);
    digitalWrite(pin_LedD4, 1);
    break;
  }

  digitalWrite(pin_PR_Latch, HIGH);

  timerRestart(My_timer);
  segDisp.vystupEX();
  mot.work = false;
  }
}

String ssid ;
String password ;

// WebServer server(80);
AsyncWebServer server(80);
AsyncWebSocket ws("/ws");
String message = "";


void MotorStopAll() // Vždy zastaví chod robota.
{
  String aaa;
  for (int i = 0; i < 8; i++)
  {
    mot.input(i);
    aaa += SendSystem.motor(i,0);
  }
  ws.textAll(aaa);
}


// Get Slider Values
String getSliderValues(int index = 100)
{
  String st;
  if (index == 100)
  {
    for (size_t i = 0; i < 8; i++)
    {
      st += SendSystem.motor(i,mot.outProc(i) );
      //st += ";m:" + String(i) + ':'+String(sliderValue[i]);
    }
  }
  else if(index >= 0 && index < 8)
  {
    st = SendSystem.motor(index,mot.outProc(Prevodnik[index]) );
  }

  return st;
}

void initFS()
{
  if (!SPIFFS.begin())
  {
    Serial.println("An error has occurred while mounting SPIFFS");
  }
  else
  {
    Serial.println("SPIFFS mounted successfully");
  }
}

double mapd(double x, double in_min, double in_max, double out_min, double out_max) {
 /* Serial.println(x);
  Serial.println(in_min);
Serial.println(in_max);
  Serial.println(out_min);
Serial.println(out_max);
Serial.println((x - in_min) * (out_max - out_min) / (in_max - in_min) + out_min);*/
    return (x - in_min) * (out_max - out_min) / (in_max - in_min) + out_min;
}

#define motRychRovne 1
#define motRychStrana 0.35

double rozdilPravy(int uhel)
{
  int uhelRozdil = uhel % 360;
    if(uhelRozdil < 0)
    {
        uhelRozdil = uhelRozdil + 360;
    }

    if(uhelRozdil >= 0 && uhelRozdil <= 90)
    {
        return mapd(uhelRozdil, 0,90,-motRychStrana,motRychRovne);
    }
    else if(uhelRozdil > 90 && uhelRozdil <= 180)
    {
        return mapd(uhelRozdil,90,180,motRychRovne,motRychStrana);
    }
    else if(uhelRozdil > 180 && uhelRozdil <= 270)
    {
        return mapd(uhelRozdil,180,270,motRychStrana,-motRychRovne);
    }
    else if(uhelRozdil > 270 && uhelRozdil <= 360)
    {
        return mapd(uhelRozdil,270,360,-motRychRovne,-motRychStrana);
    }
    return 0;
}


double rozdilLevy(int uhel)
{
    int uhelRozdil = uhel % 360;
    if(uhelRozdil < 0)
    {
        uhelRozdil = uhelRozdil + 360;
    }

    if((uhelRozdil >= 0 && uhelRozdil <= 90))
    {
        return mapd(uhelRozdil, 0,90,motRychStrana,motRychRovne);
    }
    else if(uhelRozdil > 90 && uhelRozdil <= 180)
    {
        return mapd(uhelRozdil,90,180,motRychRovne,-motRychStrana);
    }
    else if(uhelRozdil > 180 && uhelRozdil <= 270)
    {
        return mapd(uhelRozdil,180,270,-motRychStrana,-motRychRovne);
    }
    else if(uhelRozdil > 270 && uhelRozdil <= 360)
    {
        return mapd(uhelRozdil,270,360,-motRychRovne,motRychStrana);
    }
    return 0;
}


int joysticZaok(int i, int mez = 10)
{
  if (abs(i) < mez)
  {
    return 0;
  }
  else if (i > 100)
  {
    return 100;
  }
  else if (i < (-100))
  {
    return i;
  }
  return i;
}

String joysticWork(int x,int mot_x, int y, int mot_y, int rozdil = 1)
{
  String i;
  int mx = Prevodnik[mot_x];
  int my = Prevodnik[mot_y];
  if (abs(x - mot.outProc(mx)) >= rozdil)
  {
    mot.inputProc(mx,x);
    i += SendSystem.motor(mx,mot.outProc(mx) );
  }
  if (abs(y - mot.outProc(my)) >= rozdil)
  {
    mot.inputProc(my,y);
    i += SendSystem.motor(my,mot.outProc(my) );
  }
  return i;
}

String joystickRizeni(int osa_x, int osa_y)
{
  int osa_x_zaok2 = joysticZaok(osa_x);
  int osa_y_zaok2 = joysticZaok(osa_y);
  double d = sqrt((double)(osa_x_zaok2 * osa_x_zaok2 + osa_y_zaok2 * osa_y_zaok2));
  if (d > 100.0)
  {
    d = 100.0;
  }
  else if (d < 20)
  {
    d = 0.0;
  }
  double M_Levy_lokal = 0;
  double M_Pravy_lokal = 0;
  if (d != 0.0)
  {
    double rad = atan2(osa_y_zaok2,osa_x_zaok2);
    double uhel = (-180/PI)* rad;
    M_Levy_lokal = d * rozdilLevy(uhel);
    M_Pravy_lokal = d * rozdilPravy(uhel);
  }
  return joysticWork(M_Levy_lokal,M_Levy,M_Pravy_lokal,M_Pravy);
}

String joystickAllWork(int joy,int osa_x, int osa_y, int tl)
{
  int osa_x_zaok = joysticZaok(osa_x);
  int osa_y_zaok = joysticZaok(osa_y);
  switch (joy)
  {
  case 1:
  {
    return joystickRizeni(osa_x, osa_y);
    break;
  }
  case 2:
    return joysticWork(osa_x_zaok,M_1,-osa_y_zaok,M_2);
    break;
  case 3:
    return joysticWork(osa_x_zaok,M_LED,-osa_y_zaok,M_3);
    break;
  case 4:
    return joysticWork(osa_x_zaok,M_Kleste,-osa_y_zaok,M_4);
    break;        
  default:
    break;
  }
}

void ZpracovaniDat(String mess, AsyncWebSocketClient *client = NULL)
{
    komunProtokol komP;
    komP.begin(mess);
    //Serial.println("mess:");Serial.println(mess);
    String outAll;
    String outClient;
    for (int s = 0; s < komP.pocetSouboru; s++)
    {
      String souName = komP.readStr();
      int cisloM;
      int smer;
      switch (souName.charAt(0))
      {
      case 'c':
      {
        if (komP.pocetVAktualSouboru() != 2)
        {
          Serial.println("Problem s velikosti c:");
          Serial.println(komP.pocetVAktualSouboru());
          return;
        }
        String llll = komP.readStr();
        if(cons.isPrikaz(llll))
        {
          outClient += SendSystem.chat(cons.work("",client));
        }
        else{
          outAll += komP.sendAktSoubor();
          segDisp.addText4(llll,5000);
        }
        
        
      }
      break;
      case 'J':
        if (komP.pocetVAktualSouboru() != 13)
        {
          Serial.println("Problem s velikosti J:");
          Serial.println(komP.pocetVAktualSouboru());
          return;
        } 
        outAll += komP.sendAktSoubor();
        Serial.println(komP.sendAktSoubor()); 
        for (int j = 0; j < 4; j++)
        {
        int osa_x = komP.readInt();
        int osa_y = komP.readInt();
        int tl = komP.readInt();
        outAll += joystickAllWork(j + 1,osa_x, osa_y,tl);
        }
            

      break;
      case 'j':
      {
        if (komP.pocetVAktualSouboru() != 5)
        {
          Serial.println("Problem s velikosti j:");
          Serial.println(komP.pocetVAktualSouboru());
          return;
        }
        outAll += komP.sendAktSoubor();
        Serial.println(komP.sendAktSoubor());
        
        int joy = komP.readInt();
        Serial.println(joy);
        int osa_x = komP.readInt();
        int osa_y = komP.readInt();
        int tl = komP.readInt();
        outAll += joystickAllWork(joy,osa_x, osa_y,tl);
      }
      break;
      case 'm':

        if (komP.pocetVAktualSouboru() != 3)
        {
          Serial.println("Problem s velikosti M:");
          Serial.println(komP.pocetVAktualSouboru());
          return;
        }
        cisloM = komP.readInt();
        smer = komP.readInt();
        /*Serial.print("c:");Serial.println(cisloM);Serial.print("h:");Serial.println(smer);*/
        mot.inputProc(Prevodnik[cisloM], smer);
        outAll += komP.sendAktSoubor();
        break;
      case 'M':
        if (komP.pocetVAktualSouboru() != 2)
        {
          Serial.println("Problem s velikosti M:");
          Serial.println(komP.pocetVAktualSouboru());
          return;
        }
        outClient += getSliderValues(komP.readInt());
        break;
      case 'A':
        if (komP.pocetVAktualSouboru() != 1)
        {
          Serial.println("Problem s velikosti M:");
          Serial.println(komP.pocetVAktualSouboru());
          return;
        }
        outClient += getSliderValues();
        break;
      default:
        Serial.println("neznama vec");
        Serial.println(souName.charAt(0));
        outAll += getSliderValues();
        break;
      }
    }
    //Serial.println("outAll:");Serial.println(outAll);
    if (outAll != "")
    {
      ws.textAll(outAll);
    }
    //Serial.print("outClient:");Serial.println(client->id());Serial.println(outClient);
    if (outClient != "" && client != NULL)
    {
      client->text(outClient);
    }
}


void handleWebSocketMessage(void *arg, uint8_t *data, size_t len, AsyncWebSocketClient *client)
{
   AwsFrameInfo *info = (AwsFrameInfo *)arg;
   /*
     Serial.println(" Note: Applications will only see WS_TEXT and WS_BINARY.");
     Serial.println(" All other types are handled by the library. ");
    Serial.println(info->message_opcode);
    Serial.println(" Frame number of a fragmented message. ");
    Serial.println( info->num);
    Serial.println("Is this the last frame in a fragmented message ?");
    Serial.println(info->final);
    Serial.println("Is this frame masked? ");
    Serial.println(info->masked);
    Serial.println(" Message type as defined by enum AwsFrameType.\nThis value is the same as message_opcode for non-fragmented\nmessages, but may also be WS_CONTINUATION in a fragmented message. ");
    Serial.println(info->opcode);
    Serial.println("Length of the current frame.\nThis equals the total length of the message if num == 0 && final == true ");
    Serial.println( info->len);
    Serial.println(" Mask key ");
    Serial.println(info->mask[0]);Serial.println(info->mask[1]);Serial.println(info->mask[2]);Serial.println(info->mask[3]);
    Serial.println(" Offset of the data inside the current frame. ");
    Serial.println(info->index);
*/

 
  if (info->final && info->index == 0 && info->len == len && info->opcode == WS_TEXT)
  {
    data[len] = 0;
    message = (char *)data;
    ZpracovaniDat(message, client);
  }
}

void PrClent(IPAddress ip)
{
  segDisp.addText4IP(ip,2000);
  segDisp.addText4("Cl"+String(pocetClientu));
}

void onEvent2(AsyncWebSocket *server, AsyncWebSocketClient *client, AwsEventType type, void *arg, uint8_t *data, size_t len)
{
  switch (type)
  {
  case WS_EVT_CONNECT:
    Serial.printf("WebSocket client #%u connected from %s\n", client->id(), client->remoteIP().toString().c_str());
    segDisp.addText4("ConC",1000);
    pocetClientu ++;
    PrClent(client->remoteIP());
    break;
  case WS_EVT_DISCONNECT:
    Serial.printf("WebSocket client #%u disconnected\n", client->id());
    segDisp.addText4("DisC",1000);
    pocetClientu --;
    PrClent(client->remoteIP());
    break;
  case WS_EVT_DATA:
    handleWebSocketMessage(arg, data, len, client);
    break;
  case WS_EVT_PONG:
  Serial.printf("Ping from %s\n", client->remoteIP().toString().c_str());
    segDisp.addText4("ping",1000);
    PrClent(client->remoteIP());
  case WS_EVT_ERROR:
  Serial.printf("errr from %s\n", client->remoteIP().toString().c_str());
    segDisp.addText4("errr",1000);
    PrClent(client->remoteIP());
    break;
  }
}

void initWebSocket()
{
  ws.onEvent(onEvent2);
  server.addHandler(&ws);
}

void inline addWifi(String ssid, String password)
{
  preferences.putString(ssid.c_str(), password);
}

String inline getPassswordWifi(String ssid, String WNPass = WifiNotPassword)
{
  return preferences.getString(ssid.c_str(), WNPass);
}

bool inline isSaweWifi(String ssid)
{
  return preferences.isKey(ssid.c_str());
}

void MenuWifiAdd(komunFace komF)
{
  int p;
  do
  {
    segDisp.del();
    segDisp.addText4Char('.','.','.','.');
    menu w;
    w.begin(komF,"Saznam Wifi",5000);
    int n = WiFi.scanNetworks();
    for (int i = 0; i < n; i++)
    {
      Serial.print(i);
      Serial.print(": ");
      Serial.print(WiFi.SSID(i));
      Serial.print(" (");
      Serial.print(WiFi.RSSI(i));
      Serial.print(")");
      Serial.println((WiFi.encryptionType(i) == WIFI_AUTH_OPEN)?" ":"*");
      w.addPolozkaData(i,i+100,WiFi.SSID(i),500*WiFi.SSID(i).length());
    }
    w.addPolozkaData(-1,-1,"_upd",2000);
    w.addPolozkaData(-2,-2,"_clo",2000);
    p = w.work();
    if (p >= 100)
    {
      addWifi(WiFi.SSID(p-100),"");
    }
    else if (p >= 0)
    {
      String heslo = editText.WriteTextVyber("_");
      if (heslo != "" && heslo != "_")
      {
        addWifi(WiFi.SSID(p),heslo);
      }
      else
      {
        p = -1;
      }
    }
  } while (p == -1);
}

void MenuWifiSet(komunFace komF)
{
  int p;
  do
  {
    segDisp.del();
    segDisp.addText4Char('.','.','.','.');
    menu w;
    w.begin(komF,"UrciWifi",3000);
    int n = WiFi.scanNetworks();
    int swifi = 0;
    int swifiI = 0;
    for (int i = 0; i < n; i++)
    {
      Serial.print(i);
      Serial.print(": ");
      Serial.print(WiFi.SSID(i));
      Serial.print(" (");
      Serial.print(WiFi.RSSI(i));
      Serial.print(")");
      Serial.print((WiFi.encryptionType(i) == WIFI_AUTH_OPEN)?" ":"*");
      if(isSaweWifi(WiFi.SSID(i)))
      {
        w.addPolozkaData(i,i,String(WiFi.SSID(i)),2000);
        Serial.println("+");
        swifi ++;
        swifiI = i;
      }
    }
    w.addPolozkaData(-1,-1,"_upd",2000);
    w.addPolozkaData(-2,-2,"_add",2000);
    if (swifi == 1)
    {
      p = w.work(5000,swifiI);
    }
    else
    {
      p = w.work();
    }


    if(p == -2)
    {
      MenuWifiAdd(komF);
      p = -1;
    }
    else if (p >= 0)
    {
      ssid = WiFi.SSID(p);
      password  = getPassswordWifi(ssid);
    }
  } while (p == -1);
}


void setup()
{
  // put your setup code here, to run once:
  
  pinMode(pin_PR_Clock, OUTPUT);
  pinMode(pin_PR_Data1, OUTPUT);
  pinMode(pin_PR_Data2, OUTPUT);
  pinMode(pin_PR_Latch, OUTPUT);

  pinMode(pin_LedD1, OUTPUT);
  pinMode(pin_LedD2, OUTPUT);
  pinMode(pin_LedD3, OUTPUT);
  pinMode(pin_LedD4, OUTPUT);
  digitalWrite(pin_LedD1, 1);
  digitalWrite(pin_LedD2, 1);
  digitalWrite(pin_LedD3, 1);
  digitalWrite(pin_LedD4, 1);
  Serial.begin(9600);
  Serial.println("Inicializace pinu");
  segDisp.begin(&Serial, B00000001, B00000100, B00010000, B01000000, B00100000, B00000010, B00001000, B10000000);
  Serial.println("Displaj.begin");
  // zahajeni ...
  
  My_timer = timerBegin(0, 80, true);
  timerAttachInterrupt(My_timer, &HlavniPreruseni, true);
  timerAlarmWrite(My_timer, 5000, true);
  timerAlarmEnable(My_timer); // Just Enable
  
  Serial.println("Inicializace a spusteni hlavniho presuseni");
  mot.beginStart();
  mot.beginTimer();

  for (byte i = 0; i < 8; i++)
  {
    mot.begin(Prevodnik[i],  NastMotPin[Prevodnik[i]], NastMotLEDC_CHANNEL[Prevodnik[i]], NastMotInverz[Prevodnik[i]], NastMotNeg[i], NastMotMaxMin[i][0], NastMotMaxMin[i][1]);
  }

  if (mot.beginEnd() == 0)
  {
    segDisp.addText4("Err Motor");
  }

  MotorStopAll();

  Serial.println("Motor");

  enk.begin(pin_EnkA, pin_EnkB, pin_EnkDP, pin_Tlac);

  komunFace komF;
  komF.displej = &segDisp;
  komF.enk = &enk;
  komF.ser = &Serial;

  editText.begin(komF);
  
  menu Vr1;
  Vr1.begin(komF);
   
  if (!SPIFFS.begin(true))
  {
    Serial.println("An Error has occurred while mounting SPIFFS");
    return;
  }
Serial.println("Dalsi Inicailizace");

/*
  File setWeb0 = SPIFFS.open("/setWeb0.txt");
  File setWeb1 = SPIFFS.open("/setWeb1.txt");
  File setWeb2 = SPIFFS.open("/setWeb2.txt");
  File setWeb3 = SPIFFS.open("/setWeb3.txt");
  File setWeb4 = SPIFFS.open("/setWeb4.txt");
  File setWeb5 = SPIFFS.open("/setWeb5.txt");
  File setWeb6 = SPIFFS.open("/setWeb6.txt");
  File setWeb7 = SPIFFS.open("/setWeb7.txt");
*/
  preferences.begin("credentials", false);
Serial.println("Soubory");
  initFS();
  WiFi.mode(WIFI_STA);
  Serial.println("WIFI_STA");
  MenuWifiSet(komF);
  password.remove(password.length()-1);//Upravuje heslo, odstaranuje char 13 z konce
  WiFi.begin(ssid.c_str(), password.c_str());
  // Wait for connection
  Serial.println("Pripojovani se");
  Serial.println();
  byte teckyCekani=0;
  while (WiFi.status() != WL_CONNECTED)
  {
    delay(100);
    Serial.print(".");
    segDisp.addText4(" ",0,segDisp.BitSet(3-(teckyCekani % 4)));
    teckyCekani++;
  }
  Serial.println("");
  Serial.print("Connected to ");
  Serial.println(ssid);
  Serial.print("IP address: ");
  Serial.println(WiFi.localIP());
  segDisp.addText4IP(WiFi.localIP(),10000);
  initWebSocket();
  Serial.println("initWebSocket");

  server.on("/", HTTP_GET, [](AsyncWebServerRequest *request)
            { request->send(SPIFFS, "/index.html", "text/html"); });

  server.on("/reset", HTTP_GET, [](AsyncWebServerRequest *request)
            {
    MotorStopAll();
    server.reset();
    MotorStopAll(); });
  server.on("/stop", HTTP_GET, [](AsyncWebServerRequest *request)
            { MotorStopAll(); });

  server.on("/test", HTTP_GET, [](AsyncWebServerRequest *request)
            { request->send(SPIFFS, "/joy.html", "text/html"); });
  server.serveStatic("/", SPIFFS, "/");
  AsyncElegantOTA.begin(&server); // Start ElegantOTA
  server.begin();
  Serial.println("HTTP server started");
}


void loop(void)
{
  int e = enk.Enk();
  if (e != 0)
  {
    if (e == 1)
    {
      posunIP ++;
    }
    else if (e == -1)
    {
      posunIP --;
    }
    segDisp.addText4IPIndex(posunIP%4,WiFi.localIP());    
  }
  
  // Až dokončím komunikační protokol, bude fungovat zastavovaní brždění
  String p;
  for (int i = 0; i < 8; i++)
  {
    if (mot.TStop(i) != 0)
    {
      if (mot.TStop(i) < millis())
      {
        mot.input(i, mStop);
        p += SendSystem.motor(i,0);
      }
    }
  }
  if (p.length() != 0)
  {
    ws.textAll(p);
  }

  String l ;

  for (int i = 0; i < 8; i++)
  {
    //Oprava chyby, kdy knihovna říka, že motor jede při nulové rychlosti a motor se pohybuje.
    //Vznik teto nulové chyby nepodařilo vyřešit ani zaokrouhlovacím systémem
    if ((mot.outSmer(i) == mVpred ||mot.outSmer(i) == mVzad) && mot.outSpead(i) == 0)
    {
        mot.input(i, mStop);
        l += SendSystem.motor(i,0);
    }
  }
  if (l.length() != 0)
  {
    ws.textAll(l);
  }

  if(!WiFi.isConnected())
  {
    for (int i = 9; i > 0; i--)
    {
      segDisp.addText4("ECW" + String(i));
      delay(1000);
    }

    ESP.restart();
  }

  ws.cleanupClients();
}

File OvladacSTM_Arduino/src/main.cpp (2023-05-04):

//https://primalcortex.wordpress.com/2020/10/11/stm32-blue-pill-board-arduino-core-and-usb-serial-output-on-platformio/
#include <Arduino.h>
#include <komunProtokol.h>


#define J1x PA1
#define J1y PA0
#define J1t PB0
#define J2x PA3
#define J2y PA2
#define J2t PB1
#define J3x PA5
#define J3y PA4
#define J3t PB10
#define J4x PA7
#define J4y PA6
#define J4t PB11

#define ledPin PC13 //13

#define J1 0
#define J2 1
#define J3 2
#define J4 3


const int zmena = 2;
const int nullDet = 20;


#define Jx 1
#define Jy 0
#define Jt 2
const int polePinu[4][3] = {
  {J1x,J1y,J1t},
  {J2x,J2y,J2t},
  {J3x,J3y,J3t},
  {J4x,J4y,J4t}
};

#define Jx_min 0
#define Jx_max 1
#define Jx_stred 2
#define Jx_stred_max 3
#define Jx_stred_min 4
#define Jx_hod 5

#define Jy_min 6
#define Jy_max 7
#define Jy_stred 8
#define Jy_stred_max 9
#define Jy_stred_min 10
#define Jy_hod 11

#define Jt_hod 12
#define Jx_To_Jy 6

#define deatZone 0.05


int poleSys[4][13]
{
  {0,0,0,0,0,0,0,0,0,0,0,0,0},
  {0,0,0,0,0,0,0,0,0,0,0,0,0},
  {0,0,0,0,0,0,0,0,0,0,0,0,0},
  {0,0,0,0,0,0,0,0,0,0,0,0,0}
};

#define SendOldJx 0
#define SendOldJy 1
#define SendOldJt 2

int sendOld[4][3]
{
  {0,0,0},
  {0,0,0},
  {0,0,0},
  {0,0,0}
};


void SendPrint(String a)
{
  Serial.print(a);
  Serial1.print(a);
}


void SendPrintln(String a)
{
  Serial.println(a);
  Serial1.println(a);
}


typedef double resDuty;


resDuty mapD(resDuty x, resDuty in_min, resDuty in_max, resDuty out_min, resDuty out_max)
{
    return (x - in_min) * (out_max - out_min) / (in_max - in_min) + out_min;
}

int AnalogToProc(int j, int i = 0)
{
  if((poleSys[j][Jx_stred_max+i] >= poleSys[j][Jx_hod+i]) && (poleSys[j][Jx_stred_min+i] <= poleSys[j][Jx_hod+i]))
  {
    return 0;
  }
  else if(poleSys[j][Jx_hod+i] > poleSys[j][Jx_stred+i])
  {
    return mapD(poleSys[j][Jx_hod+i], poleSys[j][Jx_stred_max+i],poleSys[j][Jx_max+i],0,100);
  }
  else
  {
    return -100 + mapD(poleSys[j][Jx_hod+i], poleSys[j][Jx_min+i],poleSys[j][Jx_stred_min+i],0,100);
  }
  return 0;
}


void deatZoneVypocet(int j, int i = 0)
{
  poleSys[j][Jx_stred_max+i] = poleSys[j][Jx_stred+i] + (poleSys[j][Jx_max+i] - poleSys[j][Jx_stred+i])*deatZone;
  poleSys[j][Jx_stred_min+i] = poleSys[j][Jx_stred+i] + (poleSys[j][Jx_min+i] - poleSys[j][Jx_stred+i])*deatZone;
}


void kontrol(int j, int x, int y)
{
  if ( poleSys[j][Jx_min] > x)
  {
    poleSys[j][Jx_min] = x;
    deatZoneVypocet(j);
  }
  else if ( poleSys[j][Jx_max] < x)
  {
    poleSys[j][Jx_max] = x;
    deatZoneVypocet(j);
  }

  if ( poleSys[j][Jy_min] > y)
  {
    poleSys[j][Jy_min] = y;
    deatZoneVypocet(j,Jx_To_Jy);
  }
  else if ( poleSys[j][Jy_max] < y)
  {
    poleSys[j][Jy_max] = y;
    deatZoneVypocet(j,Jx_To_Jy);
  }
}


void Novy()
{
  bool vystup[4];
  int vystuppocet = 0;
  for (int j = 0; j < 4; j++)
  {
    int x = analogRead(polePinu[j][Jx]);
    int y = analogRead(polePinu[j][Jy]);
    int t = digitalRead(polePinu[j][Jt]);

    kontrol(j,x,y);
    poleSys[j][Jx_hod] = x;
    poleSys[j][Jy_hod] = y;
    poleSys[j][Jt_hod] = t;



    int X = AnalogToProc(j);
    int Y = (-1)*AnalogToProc(j,Jx_To_Jy);
    int T = 1-t;
    //delay(1000);
    /*
    Serial.println(j);
    Serial.println(X);
    Serial.println(Y);
    Serial.println(T);
    */

    if (abs(X - sendOld[j][SendOldJx]) > zmena || abs(Y - sendOld[j][SendOldJy]) > zmena || abs(T - sendOld[j][SendOldJt]) == 1)
    {
      vystup[j]=true;
      vystuppocet ++;

      sendOld[j][SendOldJx] = X;
      sendOld[j][SendOldJy] = Y;
      sendOld[j][SendOldJt] = T;
      
    }
    else
    {
      vystup[j]=false;
    }
  }
  //Serial.println(vystuppocet);
  if (vystuppocet == 4)
  {
    Serial.print(
      SendSystem.joysticStart() +
      SendSystem.joystickAll(
      sendOld[J1][SendOldJx],sendOld[J1][SendOldJy],sendOld[J1][SendOldJt],
      sendOld[J2][SendOldJx],sendOld[J2][SendOldJy],sendOld[J2][SendOldJt],
      sendOld[J3][SendOldJx],sendOld[J3][SendOldJy],sendOld[J3][SendOldJt],
      sendOld[J4][SendOldJx],sendOld[J4][SendOldJy],sendOld[J4][SendOldJt]  
      )
      + SendSystem.joysticStop());
  }
  else if(vystuppocet >= 1)
  {
    String pl = SendSystem.joysticStart();
    for (int j = 0; j < 4; j++)
    {
      if(vystup[j])
      {
        pl += SendSystem.joystic(j+1,sendOld[j][SendOldJx],sendOld[j][SendOldJy],sendOld[j][SendOldJt]);
      }
    }
    Serial.print(pl + SendSystem.joysticStop());
  }
  /*
Serial.println();
  for (int a = 0; a < 4; a++)
  {
    for (int b = 0; b < 13; b++)
    {
      Serial.print(poleSys[a][b]);
      Serial.print(',');
    }
    Serial.println();
  }

    for (int a= 0; a < 4; a++)
  {
    for (int b= 0; b < 3;b++)
    {
      Serial.print(sendOld[a][b]);
      Serial.print(',');
    }
    Serial.println();
  }
  */
}


void setup() {
  // put your setup code here, to run once:
  Serial1.begin(19200); // PA10  (RX) PA9 (TX) 
  pinMode(ledPin,OUTPUT);
  digitalWrite(ledPin, HIGH);
  //Android pomoci CDC
  analogReadResolution(12);
  Serial.begin(115200);
  Serial.dtr(0);
  delay(1000);
  for (int j = 0; j < 4; j++)
  {
    int x = analogRead(polePinu[j][Jx]);
    int y = analogRead(polePinu[j][Jy]);
    poleSys[j][Jx_max] = x;
    poleSys[j][Jx_stred] = x;
    poleSys[j][Jx_min] = x;
    poleSys[j][Jx_hod] = x;
    poleSys[j][Jy_max] = y;
    poleSys[j][Jy_stred] = y;
    poleSys[j][Jy_min] = y;
    poleSys[j][Jy_hod] = y;
    deatZoneVypocet(j);
  }

  digitalWrite(ledPin, LOW);
  int timeS = millis() + 10000;
  while (millis() < timeS)
  {
    for (int j = 0; j <4; j++)
    {
      int x = analogRead(polePinu[j][Jx]);
      int y = analogRead(polePinu[j][Jy]);
      kontrol(j,x,y);
    }
    if ((( timeS - millis())%1000)< 500)
    {
      digitalWrite(ledPin, LOW);
    }
    else
    {
      digitalWrite(ledPin, HIGH);
    }
  }

  for (int j = 0; j < 4; j++)
  {
    pinMode(polePinu[j][Jt],INPUT_PULLUP);
    int t = digitalRead(polePinu[j][Jt]);
    poleSys[j][Jt_hod] = t;

    sendOld[j][SendOldJx] = 0;
    sendOld[j][SendOldJy] = 0;
    sendOld[j][SendOldJt] = 0;
  }
}


void loop() {
  digitalWrite(ledPin, HIGH);
  delay(50);
  digitalWrite(ledPin, LOW);
  delay(50);
  Novy();
}

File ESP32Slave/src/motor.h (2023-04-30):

#ifndef kn_motor
#define kn_motor

#include <Arduino.h>
#include <binary.h>
#include "esp32-hal.h"
#include "soc/soc_caps.h"
#include "driver/ledc.h"
typedef double resDuty;

#define LEDC_mTIMER              LEDC_TIMER_3
#define LEDC_mFrec              5000
#define pohonMaxHod 255

struct pohonVol
{
    volatile resDuty dutOld;
    volatile resDuty duty;
    volatile ledc_mode_t speed_mode;
    volatile ledc_channel_t channel;
    volatile uint32_t hpoint;
    volatile byte pin;
};


struct pohonSet
{
    int neg;//oto4ena svorkovnice
    int inverz;//ote4eni motoru
    resDuty max;
    resDuty min;
    byte index;
    int smer;
    long timeStop;
    ledc_timer_config_t *ledc_timer;
    ledc_channel_config_t ledc_channel;
};


#define mVpred 1
#define mVzad -1
#define mStopLow 0
#define mStopHigh 2
#define mStop mStopLow
#define mBrzda 3
#define rychModLow 0
#define rychModHigh 1

class motor
{
private:
    byte set = 0;
    ledc_timer_config_t defTim;
    bool setDefTimer = 0;
    const double zaokPomer = 0.999;
public:
pohonSet m[8];
volatile pohonVol v[8];
volatile byte vyst;
volatile bool work;
    resDuty mapD(resDuty x, resDuty in_min, resDuty in_max, resDuty out_min, resDuty out_max);
    int mapZaok(resDuty x, resDuty in_min, resDuty in_max, resDuty out_min, resDuty out_max);
    byte vystup();
    void beginStart();
    bool beginTimer(uint32_t frek ,ledc_timer_t _tim  ,ledc_mode_t _speadmode );
    bool begin(byte mot, int _pin, ledc_channel_t channel,bool _inverz,bool _neg, byte _max, byte _min, ledc_timer_config_t *ledc_timer );
    bool beginEnd();
    void setPWM(int i);
    void updatePWM(int i);
    void updatePWM();
    byte numToPosun(byte i);
    byte posunToNum(byte i);
    bool inputProc(byte mot, float proc);
    bool input(byte mot, int smer ,byte spead,int maxSpead ,int minSpead , int cas );
    long TStop(byte mot);
    int outSmer(byte mot);
    int outSpead(byte mot,int min, int max );
    int outProc(byte mot);
    int maxView();
    bool maxSet(int _max);
    
};


inline byte motor::vystup()
{
    return vyst;
}


inline byte motor::numToPosun(byte i)
{
    return B10000000 >> i;
}


inline byte motor::posunToNum(byte i)
{
    switch (i)
    {
    case B10000000:
        return 0;
        break;
    case B1000000:
        return 1;
        break;
    case B100000:
        return 2;
        break;
    case B10000:
        return 3;
        break;
    case B1000:
        return 4;
        break;
    case B100:
        return 5;
        break;
    case B10:
        return 6;
        break;
    case B1:
        return 7;
        break;
            
    default:
        break;
    }
    return 0;
}

resDuty motor::mapD(resDuty x, resDuty in_min, resDuty in_max, resDuty out_min, resDuty out_max)
{
    return (x - in_min) * (out_max - out_min) / (in_max - in_min) + out_min;
}


int motor::mapZaok(resDuty x, resDuty in_min, resDuty in_max, resDuty out_min, resDuty out_max)
{
    double o= (x - in_min) * (out_max - out_min) / (in_max - in_min) + out_min;
    int i = o;
    if(o - (double)i > zaokPomer)
    {
        i++;
    }
return i;

}

inline long motor::TStop(byte mot)
{
    return m[mot].timeStop;
}


/*
//https://github.com/espressif/esp-idf/tree/4b6d9c8ad3/examples/peripherals/ledc/ledc_basic
#define LEDC_TIMER              LEDC_TIMER_0
#define LEDC_MODE               LEDC_LOW_SPEED_MODE
#define LEDC_OUTPUT_IO          (5) // Define the output GPIO
#define LEDC_CHANNEL            LEDC_CHANNEL_0
#define LEDC_DUTY_RES           LEDC_TIMER_13_BIT // Set duty resolution to 13 bits
#define LEDC_DUTY               (4095) // Set duty to 50%. ((2 ** 13) - 1) * 50% = 4095
#define LEDC_FREQUENCY          (5000) // Frequency in Hertz. Set frequency at 5 kHz

static void example_ledc_init(void)
{
    // Prepare and then apply the LEDC PWM timer configuration
    ledc_timer_config_t ledc_timer = {
        .speed_mode       = LEDC_MODE,
        .timer_num        = LEDC_TIMER,
        .duty_resolution  = LEDC_DUTY_RES,
        .freq_hz          = LEDC_FREQUENCY,  // Set output frequency at 5 kHz
        .clk_cfg          = LEDC_AUTO_CLK
    };
    ESP_ERROR_CHECK(ledc_timer_config(&ledc_timer));

    // Prepare and then apply the LEDC PWM channel configuration
    ledc_channel_config_t ledc_channel = {
        .speed_mode     = LEDC_MODE,
        .channel        = LEDC_CHANNEL,
        .timer_sel      = LEDC_TIMER,
        .intr_type      = LEDC_INTR_DISABLE,
        .gpio_num       = LEDC_OUTPUT_IO,
        .duty           = 0, // Set duty to 0%
        .hpoint         = 0
    };
    ESP_ERROR_CHECK(ledc_channel_config(&ledc_channel));
}
*/


void motor::beginStart()
{
    vyst = 0;
    set = 0;
    setDefTimer = false;
}
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

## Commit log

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2022-05-19 Funkční ovladani vsech motorů
    Při neplém výkonu se pohybuji i ostatní motory....
2022-05-27 odladeni3
    Zkrácení synchronizačního protokolu. Přidaní dvoubarevné LED, svítí buď zelená nebo červená LED.
    POZOR: Použitím modulu L9110S měl odpor 10Kohm na VCC napájení modulu, to způsobile poškození ESP32.
    OPRAVA: Nové ESP32, Předělání na jiný typ. Odpájení zmíněných odporů z modulů. Modul spíná už kolem 2V.
    DOPORUČENÍ: Z modulu L9110S odpájejte rezistory mezi řídicími piny a napájením....
2022-05-29 PripravaNa3Dtisk
    Vkládám materiály pro 3D tisk.
    [Engrenage.stl, Kolo.scad, Kolo10mm4krat.stl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]
2022-05-30 ZmenaPozdvozku
    V konfiguraci 2x2 motoru se v podstatě nedalo otáčet. Vyměnil jsem přední kola za otočná kola umístěná na podvozku.
    [Kolo.scad, Kolo10mm4krat.stl, Kolo4mm4krat.stl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]
2022-05-30 Uprava_klesti
    Přidány botce směrem dolů.
    [kleste.scad, kleste.stl]
2022-06-01 Zmena 3D tisku
    [kleste.scad, kleste2.stl, kleste3.stl]
2022-06-01 zmena tisku 2
    [kleste.scad, kleste4.stl]
2022-06-01 zmena tisku 3
    [kleste.scad, kleste5.stl]
2022-06-09 Oprava Redukce podle reality.
    [kleste.scad]
2022-11-11 Přidaní PCB
    zatím čekám na vyfrézovaní
    [Drill_NPTH_Through.DRL, Drill_PTH_Through.DRL, Drill_PTH_Through_Via.DRL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]
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2022-12-08 Vyřešeno, ale je zde jiná výjimka
    Spouštění při rychlém otáčení enkodéru:
    Guru Meditation Error: Core 1 panic'ed (Interrupt wdt timeout on CPU1).
2022-12-08 Revert "Spatny napad"
    This reverts commit 3f2e9e605b6d3a5556171ec896e4470db4e6f34a.
    [disp.h, motor.h]
2022-12-08 Revert "Rozdělení souboru "menu.h" na "menu.h" a "writeTextSegDisp.h""
    This reverts commit 09ea711a861a2bf1c010425451eafc38b0ec183a.
    [main.cpp]
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2022-12-12 Novy hardware
    [Drill_NPTH_Through.DRL, Drill_PTH_Through.DRL, Drill_PTH_Through_Via.DRL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]
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2022-12-23 Revert "Vypisování počtu klientů."
    This reverts commit 28182a785a9ab02dbcba4cdfdf7b462d93fbb43b.
    [main.cpp]
2022-12-23 Revert "Marná snaha vylepšení enkodéru"
    This reverts commit c4cf0d325ee680f98d0132d7a03d4b369ddfaf46.
    [enkoder.h, main.cpp]
2022-12-23 Revert "Revert "Vypisování počtu klientů.""
    This reverts commit b7fb805c2df70549e6a7b30e0786e12af167f0fd.
    [main.cpp]
2023-01-06 Revert "Snaha sjednocení posílaných a přeposílaných baličku pomoci JSON"
    This reverts commit a2d6fb60ff835059bf752bd0eea52b24b2a44aef.
    [main.cpp, motor.h]
2023-01-10 Zprovoznění protokolu.
    Funguje ovládaní motoru. původní funkcionalita slideru a zobrazovače je obnovena.
2023-01-10 Větší automatizace js. Přidaní měření času.
    Zmenšení rizika chyby.
    Statistika pro posílaní hodnoty pro jeden motor:
    Čas vytvoření odesílané zprávy je maximálně 0,8ms
    Čas zkracovaní přijaté zprávy je maximálně 2,1ms
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2023-01-17 Nepochopitelná chyba
    Problém nastává někde v rámci funkce ws.textAll(outAll) , předtím jsem se nesetkal s touto chybu, ale předtím je použito client->text(outClient)
    Rozdělení posílaní zpráv mezi klienta a klienty mi mělo právě ušetřit paměť, ne že se mi vyhodí chyba popisující zaplnění paměti.
    výstup za seriálového portu:
    outAll:
    ;m:0:9;m:1:-7
    outAllp1:
    assert failed: block_locate_free heap_tlsf.c:447 (block_size(block) >= size)
    Backtrace:0x40083bb5:0x3ffd3fb00x4008bc71:0x3ffd3fd0 0x400911d1:0x3ffd3ff0 0x40090319:0x3ffd4120 0x40090b5f:0x3ffd4140 0x40090de0:0x3ffd4160 0x40083f6a:0x3ffd4180 0x40083f7d:0x3ffd41b0 0x40083fad:0x3ffd41d0 0x400911e1:0x3ffd41f0 0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
    [main.cpp]
2023-01-17 Provizorní řešení
    Po p5idan9 fince ws._cleanBuffers(); se mo objevily tyto hlášky:
    "CORRUPT HEAP: Bad head at 0x3ffd48a4. Expected 0xabba1234 got 0x00000000
    assert failed: multi_heap_free multi_heap_poisoning.c:253 (head != NULL)"
    Problém je vyřešen tím, že se každý údaj posílá zvlášť.
    Budu se tím dále zabývat....
    [main.cpp]
2023-01-19 Revert "Málo paměti."
    This reverts commit fb100efe9e4d6a0aaba1fa4c8543a855870134a4.
    [main.cpp]
2023-01-19 Revert "Návrh na změnu vstupního protokolu. Ale vracím to zpět."
    This reverts commit 9f615c0260f1257cb11de84e5dc167e4e40511db.
    [main.cpp]
2023-01-20 Aktualizace jádra ESP-Arduino
    Nutné pro další aktualizace.
    V této konfiguraci knihoven se problém ještě zhoršil.
2023-01-20 Revert "Aktualizace jádra ESP-Arduino"
    This reverts commit fe89dc808f63b06a42922e22c40eaacd19b5fcf7.
2023-01-20 Revert "Revert "Málo paměti.""
    This reverts commit ec0abbe22f7a4833822bf73f9d1c64a7071449d0.
    [main.cpp]
2023-01-22 Rychloupínák na stativ
    [Rychloupínák_na_stativ.scad]
2023-01-22 Základní tvar rychloupínaku
    [Rychloupínák_na_stativ.scad]
2023-01-22 rychloupinák přidaní děr
    [Rychloupínák_na_stativ.scad]
2023-01-22 rychloupinák v1
    [Rychloupínák_na_stativ.scad, Rychloupínák_na_stativ.stl]
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2023-01-25 Špatný návrh rychloupínaku
    Spoléhal jsem se na nevhodnou dokumentaci z internetu.
    [Rychloupínák_na_stativ.scad]
2023-01-25 Nový návrh rychoupínáku
    [Rychloupínák_na_stativ.scad, Rychloupínák_na_stativ.stl]
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2023-02-11 Přidaní knihovoarpruss/USBComposite_stm32f1
    https://github.com/arpruss/USBComposite_stm32f1
    Problem nenalezeno #include <boards.h>
    ......
    Compiling .pio\build\bluepill_f103c8\libf53\USBComposite for STM32F1\Consumer.cpp.o
    Compiling .pio\build\bluepill_f103c8\libf53\USBComposite for STM32F1\Digitizer.cpp.o
    In file included from .pio\libdeps\bluepill_f103c8\USBComposite for STM32F1\Consumer.cpp:1:
    .pio\libdeps\bluepill_f103c8\USBComposite for STM32F1\USBComposite.h:4:10: fatal error: boards.h: No such file or directory
    ****************************************************************
    * Looking for boards.h dependency? Check our library registry!
    *
    * CLI > platformio lib search "header:boa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
    [main.cpp]
2023-02-11 Revert "Přidaní knihovoarpruss/USBComposite_stm32f1"
    This reverts commit 21763171cb12718a9cada873619dd397789e4cb4.
    [main.cpp]
2023-02-11 přidaní knihovny USBSerial.h
    ...
    Compiling .pio\build\bluepill_f103c8\FrameworkArduino\stm32\OpenAMP\libmetal\generic\generic_shmem.c.o
    Compiling .pio\build\bluepill_f103c8\FrameworkArduino\stm32\OpenAMP\libmetal\generic\time.c.o
    src\main.cpp: In function 'void setup()':
    src\main.cpp:92:3: error: 'USBSerial' was not declared in this scope; did you mean 'Serial'?
    92 | USBSerial usbSerial(0x1f00, 0x2012, 0x0001, false);
    | ^~~~~~~~~
    | Serial
    Compiling .pio\build\bluepill_f103c8\FrameworkArduino\stm32\OpenAMP\libmetal\init.c.o
    *** [.pio\build\bluepill_f103c8\src\main.cpp.o] Error 1
    [main.cpp]
2023-02-11 Revert "přidaní knihovny USBSerial.h"
    This reverts commit c239d775254ab5781a4c8392d4eafdfec952a0f8.
    [main.cpp]
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2023-04-09 Přidaní 3D objektů překážek
    Některé se budou vyrábět ze dřeva a některé z plastu.
    [Auto.scad, Auto.stl, BaterieKostky.scad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]
2023-05-04 Aktualizace části překážky pojmenované jako "Značka" pro 3D tisk
    Podstava je vyrobena ze dřeva
    [Znacka.scad, Znacka.stl]
2023-05-05 kleste.scad úprava formátovaní
    [kleste.scad]
2023-05-05 Create chapadlo2023.scad
    Nové kleště pro rok 2023
    [chapadlo2023.scad]
2023-05-25 Revert "Neotestovaný funkce managerClient"
    This reverts commit 4c4c85e7b04488295c575750b5d35dbefe26ea92.
    [main.cpp, motor.h]
2023-05-25 Vytvoření souborů pro nové komponenty 3D tisku
    [Nosnik.scad, Prevodniky.scad]
2023-05-25 Zakladni nosnik
    [Prevodniky.scad]
2023-05-25 library: OpenSCAD gear generator
    https://github.com/chrisspen/gears.git
    [Prevodniky.scad, gears.scad]
2023-05-25 chyba generatoru
    [Prevodniky.scad]
2023-05-25 Revert "chyba generatoru"
    This reverts commit 7239393f49e939a41bd3cff33e3907cea26e9a46.
    [Prevodniky.scad]
2023-05-25 Use SharpCoder SharpCoder/_Gear Generator README.md
    https://gist.github.com/SharpCoder/b1cab020d2d8d7626d8556bdac7069cd
    [Prevodniky.scad, gear-generation-example.scad, gears.scad]
2023-05-25 Nosniky připraveny k tisku
    [Prevodniky text.stl, Prevodniky tisk.stl, Prevodniky.scad]
2023-05-25 Oprava: Převodníky jsou připraveny k tisku
    [Prevodniky.scad]
2023-05-25 U nosníku vymodelovaný motor
    [Nosnik.scad]
2023-05-25 NosnikA
    Jde o nosník s poslední dírou v 6 cm
    [Nosnik.scad, NosnikA.stl]
2023-05-25 NosnikB
    poslední díra je v 5cm jako originál.
    [NosnikB.scad, NosnikB.stl]
2023-05-27 Vytvoření tahla
    [tahlo.scad]
2023-05-29 oprava tahla
    [tahlo.scad, tahloOprava.stl]
2023-05-29 Vytvoření souboru pro kleště
    Vycházím ze návrhu z minulého roku
    [kleste.scad]
2023-05-29 první verze chapadla
    [kleste.scad]
2023-05-29 Dokončení a simulace kleští
    [kleste.scad, kleste.stl]
2023-05-30 Oprava klesti
    [kleste.scad, klesteOprava.stl]
2023-06-01 Zaloha staré prace na kleštích
    [kleste - kopie z 31_5_2023.scad, kleste31_5_2023.stl, klesteOprava31_5_2023.stl]
2023-06-01 Nova redukce
    [kleste.scad]
2023-06-01 vylepsena redukce
    [kleste.scad]
2023-06-01 mezi uloženi klesti
    [kleste.scad]
2023-06-01 přidaní buldozer části
    [kleste.scad]
2023-06-01 Dokončení kleští
    [kleste.scad, kleste1 6 23.stl]
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
